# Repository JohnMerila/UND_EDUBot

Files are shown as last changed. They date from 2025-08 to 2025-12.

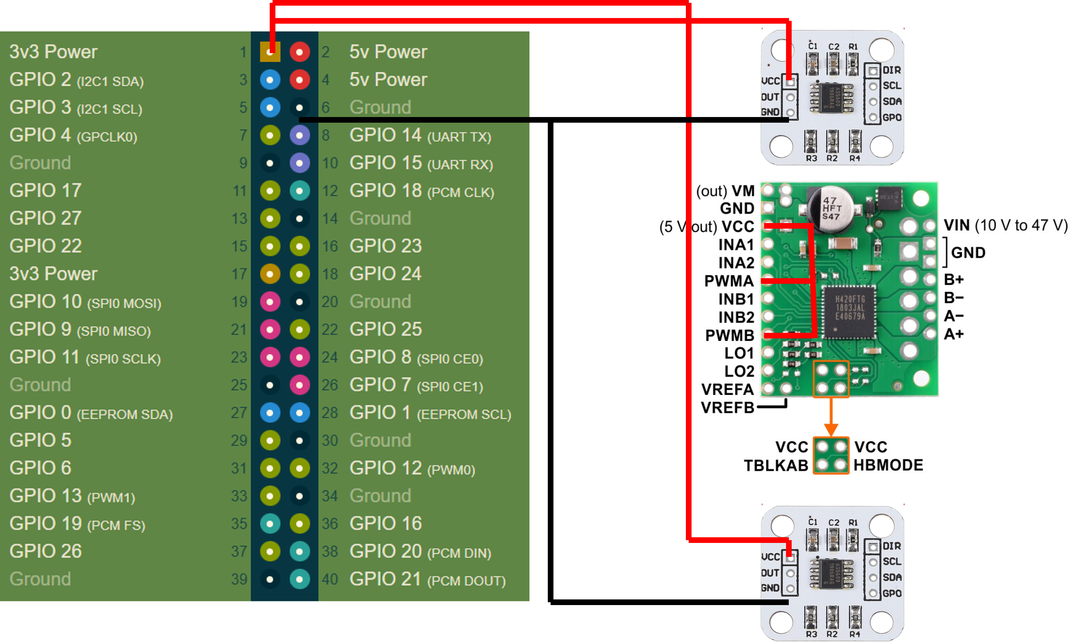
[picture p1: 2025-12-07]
docs/Photos/wiring_diagram_V1.png

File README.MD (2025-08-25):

# UND_EDUBot Overview

# Build the robot

The parts list for the is in the parts list excel file.  Purchase the needed components to build the robot.

If you are building the robot with others several people can build one robot with multi packs of screws and wire.

The CAD models for printing are found in the /build/CAD Models directory.  The .3mf files can be imported directly to the slicer of your choosing for printing.  It is reccommended to use support material, however, acceptable results can be achieved without supports.

WILL BE UPDATED: Soldering and assembly of the electrical components should be done following the wiring diagram found in the wiring diagram power point in the /build director

## Tools Needed:

- 3D printer
- Soldering iron & solder
- Metric hex key set
- Small flat head screwdriver
- Small pliers

# Build Instructions

Build instructions will be provided by youtube videos which will be posted.  Following the video instructions and diagrams provide all the information needed to build the robot.

# Powering up for the first time

Once the robot is built you can power up the pi with a flashed micro SD card.

In the /software/Pi Image directory the image for the raspberry pi is provided.

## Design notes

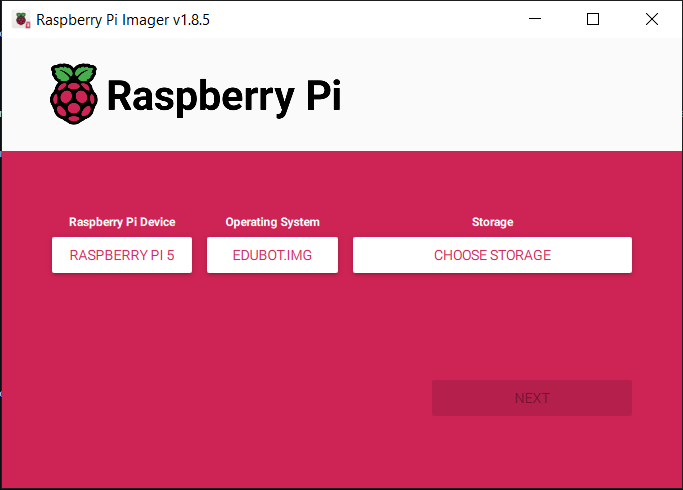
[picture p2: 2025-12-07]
docs/Photos/RPi Imager.PNG

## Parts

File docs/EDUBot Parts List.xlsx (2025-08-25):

Subsystem | Component | Number | Buy No. | Item Cost | Total Cost | Link
Drive | Motors | 2 | 2 | 12.99 | 25.98 | 163 RPM Mini Econ Gear Motor - ServoCity® (https://www.servocity.com/163-rpm-mini-econ-gear-motor/)
 | Wheels | 1 | 1 | 12 | 12 | Pololu Multi-Hub Wheel w/Inserts for 3mm and 4mm Shafts - 80×10mm, Black, 2-Pack (https://www.pololu.com/product/3690)
 | Ball Caster | 1 | 1 | 4.5 | 4.5 | Pololu Ball Caster with 3/4″ Metal Ball (https://www.pololu.com/product/955)
Electronics | Motor Controller | 1 | 1 | 12.99 | 12.99 | Pololu - TB67H420FTG Dual/Single Motor Driver Carrier (https://www.pololu.com/product/2999)
 | Encoders | 2 | 1 | 10 | 10 | Amazon.com: WWZMDiB 4Pcs AS5600 Magnetic Encoder 3.3V 12bit high Precision Magnetic Induction Angle Measurement Sensor Module，Mainly Used to Obtain Information Such as Progressive Motor Speed : Industrial & Scientific (https://www.amazon.com/WWZMDiB-Measurement-Module%EF%BC%8CMainly-Information-Progressive/dp/B0CM3C8KFT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)
 | Rpi | 1 | 1 | 80 | 80 | 2648-SC1112-ND
 | Rpi Active Cooler | 1 | 1 | 5 | 5 | 2648-SC1148-ND
 | Pi Camera | 1 | 1 | 25 | 25 | 2648-SC1223-ND
 | micro HDMI cable | 1 | 1 | 6.99 | 6.99 | Amazon.com: Amazon Basics Micro HDMI to HDMI Display Cable, 18Gbps High-Speed, 4K@60Hz, 2160p, 48-Bit Color, Ethernet Ready, 6 Foot, Black : Electronics (https://www.amazon.com/Amazon-Basics-Display-High-Speed-Ethernet/dp/B07KSDB25X?sp_csd=d2lkZ2V0TmFtZT1zcF9hdGY)
 | Gpio breakout | 1 | 1 | 10.99 | 10.99 | Amazon.com: Treedix RPi GPIO Terminal Block Breakout Board Module Expansion Board Compatible with Raspberry Pi 4B/3B+/3B/2B/Zero/Zero W : Electronics (https://www.amazon.com/Treedix-Terminal-Expansion-Compatible-Raspberry/dp/B09MFB6PJH)
 | Gpio standoff | 1 | 1 | 6.99 | 6.99 | Amazon.com: DSLRKIT 8.5mm GPIO and PoE Pin Header Height Increaser Extender for Raspberry Pi 5 4B 3B+ 3B (Pack of 2) : Electronics (https://www.amazon.com/DSLRKIT-8-5mm-Increaser-Extender-Raspberry/dp/B0F1F84GKV)
 | Lidar | 1 | 1 | 99 | 99 | 1738-1402-ND
 | 3S UPS | 1 | 1 | 32 | 32 | Amazon.com: Waveshare Uninterruptible Power Supply (UPS) Module, Supports Charging and Power Output at The Same Time, 3S & 5V 5A Output, Compatible with Raspberry Pi Board : Electronics (https://www.amazon.com/waveshare-Uninterruptible-UPS-Module-3S/dp/B0BQC2WNR8)
 | Micro USB cable | 1 | 1 | 6.99 | 6.99 | Amazon.com: Short Micro USB Cable 1ft [5 Pack] USB 2.0 Micro USB Charging Cable Android Charger Cord for Samsung Galaxy S7 Edge S6 J7 Note 5 LG Kindle Sony PS4 TV Stick Smartphones (Black) : Electronics (https://www.amazon.com/Android-Compatible-Smartphones-Charging-Stations/dp/B095JZSHXQ)
*6 for price of 3 | 18650 Battery | 3 | 1 | 20 | 20 | Amazon.com: Tokeyla 3.7 Volt 18650 Rechargeable Battery, 3000mAh Battery Flat Top Lithium Batteries for LED Flashlights, Headlamp (6 Pack) : Health & Household (https://www.amazon.com/Tokeyla-Rechargeable-Batteries-Flashlights-Headlamp/dp/B0DRCQHZRH)
 | Micro SD | 1 | 1 | 16.99 | 16.99 | Amazon.com: SanDisk 128GB Extreme microSDXC UHS-I Memory Card with Adapter - Up to 190MB/s, C10, U3, V30, 4K, 5K, A2, Micro SD Card - SDSQXAA-128G-GN6MA : Electronics (https://www.amazon.com/SanDisk-Extreme-microSDXC-Memory-Adapter/dp/B09X7BK27V)
Consumables Note* all of these are more than needed for one robot, if on campus multiple people can share parts | M4x8 | 4 | 1 | 24.98 | 24.98 | HELIFOUNER 1280 Pieces M2 M2.5 M3 M4 304 Stainless Steel Hex Socket Cap Metric Screws Bolts Washers Nuts Hardware Assortment Kit with Hex Wrenches: Amazon.com: Industrial & Scientific (https://www.amazon.com/HELIFOUNER-Stainless-Hardware-Assortment-Wrenches/dp/B09WJ14JWF)
 | M4x12 | 4 |  |  |  | This multi pack is the best way to get all you need for this robot and have extra for other projects
 | M2x8 | 8
 | M2x16 | 2 | Optional
 | M2 Nuts | 2 | Optional
 | M2.5x8 | 8
 | 24 gauge wire multi color |  | 1 | 15.99 | 15.99 | TUOFENG 24 AWG Flexible Silicone Wire, 30ft/9m Each (6 Colors), Tinned Copper Core, High Temp Resistant (-60C to +200C), Suitable for Electrical & Electronic Devices - Amazon.com (https://www.amazon.com/TUOFENG-Wire-Stranded-Flexible-Silicone-Different/dp/B07G2BWBX8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)
 | 20 gauge wire red/black |  | 1 | 10.98 | 10.98 | https://www.amazon.com/BNTECHGO-Silicone-Flexible-Strands-Stranded/dp/B07HGT7N29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
 | PLA Filament | 1
 | Small Zipties |  | 1 | 2.99 | 2.99 | Amazon.com: Zip Ties 4 inch, Small Zip Ties with 18 lb Tensile Strength, Black, 1000 Pack, by Tantti Supply : Electronics (https://www.amazon.com/Small-Tensile-Strength-Tantti-Supply/dp/B0C2KGK2HR?sp_csd=d2lkZ2V0TmFtZT1zcF9hdGY)
Optional Accessories | Small Router | 1 | 1 | 34 | 34 | Amazon.com: GL.iNet GL-AR300M16-Ext Portable Mini Travel Wireless Pocket Router - WiFi Router | OpenWrt | 2 x Ethernet Ports | OpenVPN/Wireguard VPN for Public & Hotel Wi-Fi | USB 2.0 Port | 2 x External Antennas : Electronics (https://www.amazon.com/GL-iNet-GL-AR300M16-Ext-Pre-Installed-Performance-Programmable/dp/B07794JRC5)
 |  |  |  | Total Cost | 464.36
 |  |  |  | w/o consumables | 409.42

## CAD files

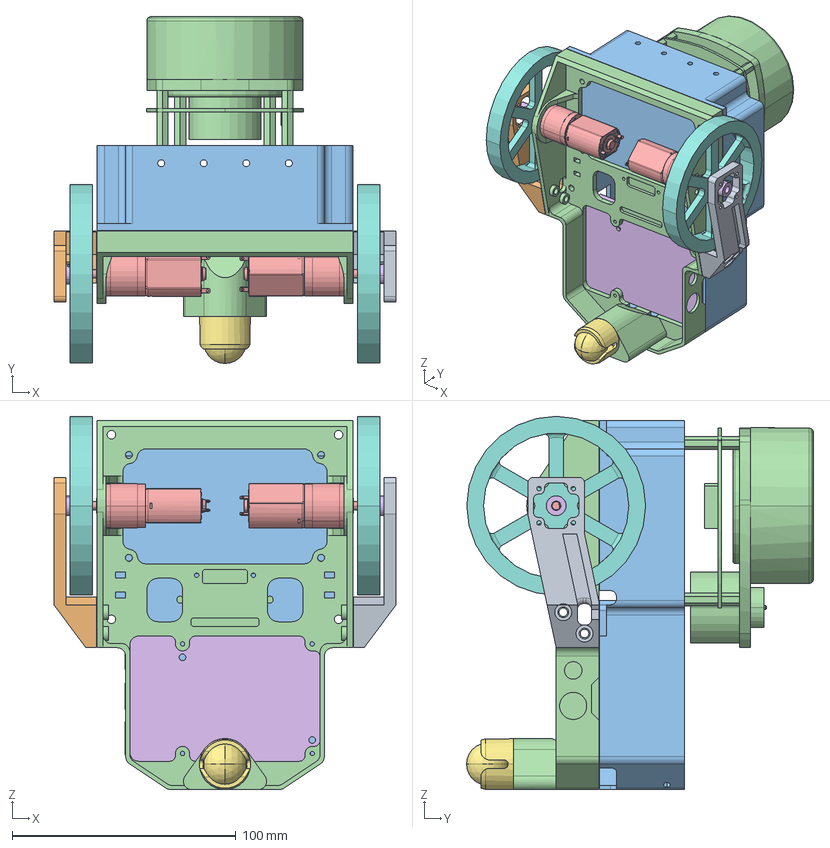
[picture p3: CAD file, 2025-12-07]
docs/Build/CAD Models/medium_assy_v2_asm.stp
152.9 x 155.2 x 167.0 mm
BODY_PLATEV2
BOSS-EXTRUDE2100
BOSS-EXTRUDE37
BOSS-EXTRUDE2300
BOSS-EXTRUDE2400
BOSS-EXTRUDE26200
12V_UPS
ENCODER_ADAPTER x 2
POLOLU-BALL-CASTER-WITH-0-750IN
POLOLU_80MM_WHEEL x 2

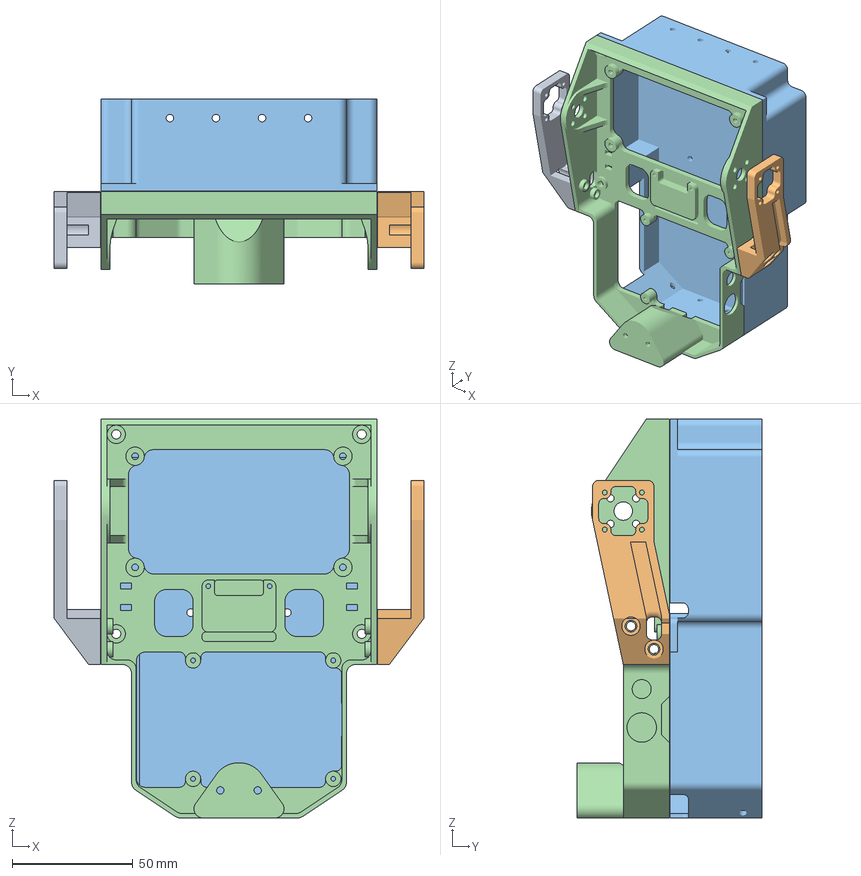
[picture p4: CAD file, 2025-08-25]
docs/Build/CAD Models/body_platev2v2.3mf
152.9 x 76.6 x 165.1 mm
BODY_PLATEV2_0_body_0
BODY_PLATEV2_0_body_1
BODY_PLATEV2_0_body_2
BODY_PLATEV2_1

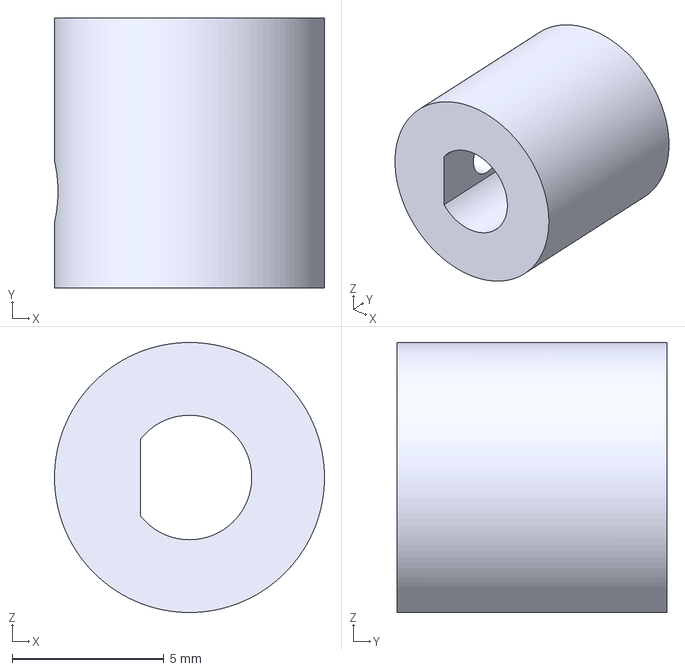
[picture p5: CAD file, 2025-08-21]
docs/Build/CAD Models/encoder_adapter.3mf
8.89 x 8.89 x 8.89 mm

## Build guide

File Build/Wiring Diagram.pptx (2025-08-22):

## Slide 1

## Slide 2

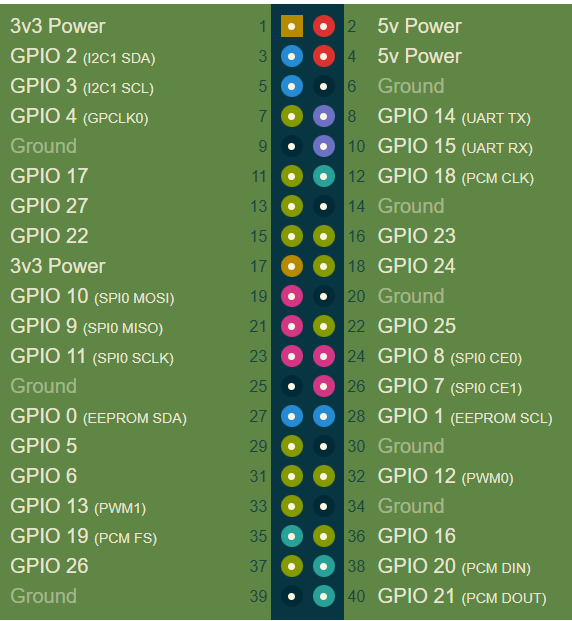
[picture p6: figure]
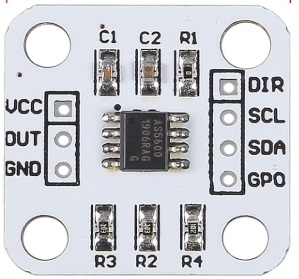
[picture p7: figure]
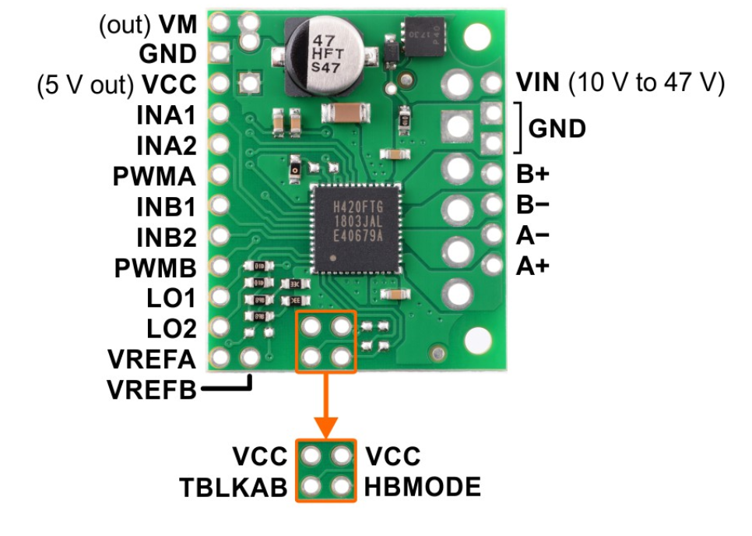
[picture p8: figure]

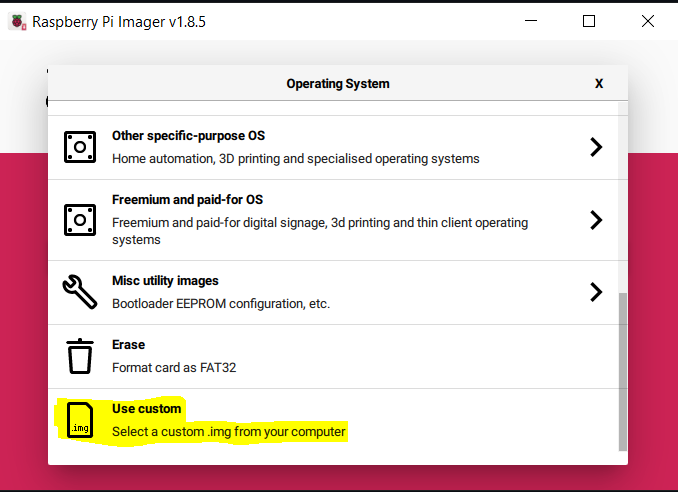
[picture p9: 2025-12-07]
docs/Photos/Operating System Selection.PNG

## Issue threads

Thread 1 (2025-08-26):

Missing "/software/Pi Image" directory

brownjordan317, 2025-08-26:
As stated in the title, the readme mentions a *.img file that should be in that directory, but no such directory exists currently

Closed 2025-09-08.

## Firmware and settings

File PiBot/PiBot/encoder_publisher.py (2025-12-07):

import rclpy
from rclpy.node import Node
from sensor_msgs.msg import JointState
import math

import smbus2
import time


# Define I2C address and bus
AS5600_ADDR = 0x36
ANGLE_REG = 0x0E




def read_angle_L():
    bus = smbus2.SMBus(1)
    # Read two bytes from the angle register
    raw_data = bus.read_i2c_block_data(AS5600_ADDR, ANGLE_REG, 2)
    angle = (raw_data[0] << 8) | raw_data[1]  # Combine MSB and LSB
    angle = angle & 0x0FFF  # Mask to 12 bits
    return (angle / 4096.0) * 360.0  # Convert to degrees

def read_angle_R():
    bus = smbus2.SMBus(4)
    # Read two bytes from the angle register
    raw_data = bus.read_i2c_block_data(AS5600_ADDR, ANGLE_REG, 2)
    angle = (raw_data[0] << 8) | raw_data[1]  # Combine MSB and LSB
    angle = angle & 0x0FFF  # Mask to 12 bits
    return (angle / 4096.0) * 360.0  # Convert to degrees


class JointStatePublisher(Node):
    def __init__(self):
        super().__init__('minimal_publisher')
        self.publisher_ = self.create_publisher(JointState, 'joint_states', 10)
        timer_period = 0.05  # seconds
        self.timer = self.create_timer(timer_period, self.encoder_callback)
        self.joint_names = ['left', 'right']
        self.ang_L_prev = read_angle_L()
        self.time_L_prev = time.time()
        self.ang_R_prev = read_angle_R()
        self.time_R_prev = time.time()
        
        
        
        self.get_logger().info('Joint State Publisher Node has been started.')

    def encoder_callback(self):
        try:
            msg = JointState()

            # Fill joint names
            msg.name = self.joint_names
            ang_L = read_angle_L()
            
            vel_L = (ang_L - self.ang_L_prev) / (time.time() - self.time_L_prev)
            self.time_L_prev = time.time()
            self.ang_L_prev = ang_L
            ang_R = read_angle_R()
            
            vel_R = (ang_R - self.ang_R_prev) / (time.time() - self.time_R_prev)
            
            self.time_R_prev = time.time()
            self.ang_R_prev = ang_R
            msg.position = [ang_L,ang_R]
            msg.velocity = [vel_L,vel_R]
            
            self.publisher_.publish(msg)
            # msg = String()
            # msg.data = 'Hello World: %d' % self.i
            # self.publisher_.publish(msg)
            # self.get_logger().info('Publishing: "%s"' % msg.data)
            # self.i += 1
        except OSError as e:
            self.get_logger().warn(f"I2C read failed: {e}")
        except Exception as e:
            self.get_logger().error(f"Unexpected error in encoder_callback: {e}")


def main(args=None):
    rclpy.init(args=args)

    minimal_publisher = JointStatePublisher()

    rclpy.spin(minimal_publisher)

    # Destroy the node explicitly
    # (optional - otherwise it will be done automatically
    # when the garbage collector destroys the node object)
    minimal_publisher.destroy_node()
    rclpy.shutdown()


if __name__ == '__main__':
    main()



# try:
#     while True:
#         angleL = read_angle_L()
#         angleR = read_angle_R()
#         print(f"Angle: {angleL:.2f} degrees")
#         print(f"Angle: {angleR:.2f} degrees")
#         time.sleep(0.05)
# except KeyboardInterrupt:
#     print("Exiting...")

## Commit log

2025-08-21 First Changes
    [EDUBot Parts List.xlsx]
2025-08-21 Files Added
    [body_platev2.3mf, encoder_adapter.3mf]
2025-08-25 Moving stuff around
    [EDUBot Parts List.xlsx]
2025-08-25 Updating CAD
    [EDUBot Parts List.xlsx, body_platev2.3mf, body_platev2v2.3mf]
2025-08-25 Updating BOM
    [EDUBot Parts List.xlsx]
